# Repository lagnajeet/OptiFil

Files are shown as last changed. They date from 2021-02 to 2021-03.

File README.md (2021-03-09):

# OptiFil
Optical Filament Sensor
<p align="center">
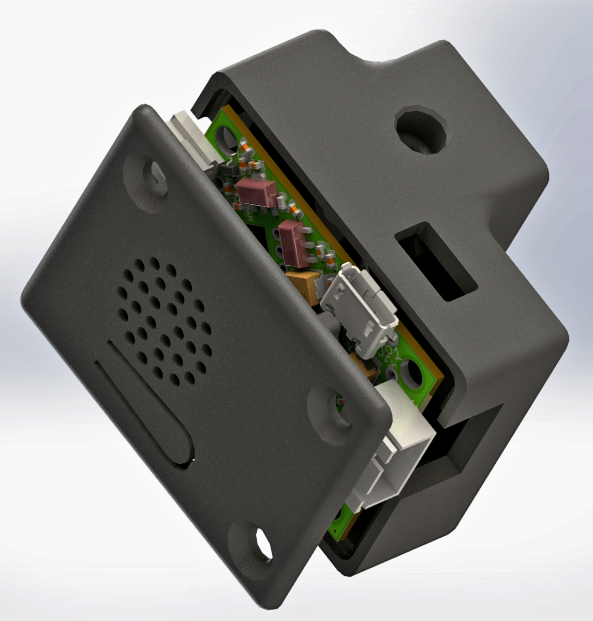
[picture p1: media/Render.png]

</p>
This filament sensor is based on the same principle that makes optical mouse work. The sennsor used in here is an ADNS9800 and the processor is an ESP8285. The filament moves infront of the optical mouse sensor and the surface property and speed of the sensor is used to determine runouts and jams.
<p align="center">

  <i>Green - Normal Operation, Red - Filament Runout, Purple - Filament Jammed</i>
</p>
The various settings of the sensor can be set from the web interface. The device exposes itself as a SSDP service.Below is a acreenshot of the web interface.
<p align="center">
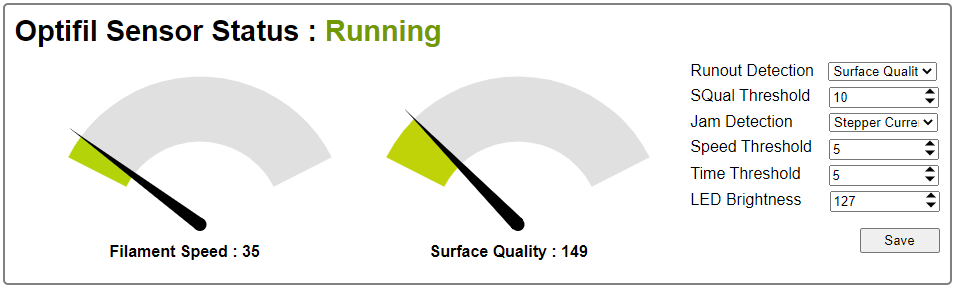
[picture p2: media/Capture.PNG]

</p>

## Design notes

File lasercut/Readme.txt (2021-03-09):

The SVG filles are for laser cutting the light guides and the edge light logo piece. The thickness of the acrylic is 2mm. The STL files are designed to take 2mm acrylics. Blacken the bottom surface with a very optically (which covers the IR range) opaque dye or material before putting the top cover.

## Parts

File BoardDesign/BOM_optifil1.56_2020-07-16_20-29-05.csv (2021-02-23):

ID | Name | Designator | Footprint | Quantity | Manufacturer Part | Manufacturer | Supplier | Supplier Part | value
1 | ESP8285_ESP-01F01F | U$3 | ESP8285-01F | 1 |  |  | LCSC |  | ESP8285_ESP-01F01F
2 | WS2812_2020 | LED3,LED4 | _2020 | 2 |  |  | LCSC
3 | SOLDERJUMPERNC | SJ1,SJ2 | SJ_2S_SMALL | 2 |  |  | LCSC |  | SOLDERJUMPERNC
4 | AVAGO_ADNS-9500 | U$1 | AVAGO_ADNS-9500 | 1 |  |  | LCSC |  | AVAGO_ADNS-9500
5 | 10u | C12,C14,C13,C15,C18,C5,C8,C6,C20,C24 | 402 | 10 |  |  | LCSC | C15525 | 10u
6 | 10k | R2,R3,R4,R1,R6,R7,R13,R14,R10,R15,R16 | 402 | 11 |  |  | LCSC | C25744 | 10k
7 | 100 | R5,R8 | 402 | 2 |  |  | LCSC | C25076 | 100
8 | JST-XH-03-PIN-ROUND-PAD | X1 | JST-XH-03-PACKAGE-ROUND-PAD | 1 |  |  | LCSC |  | JST-XH-03-PIN-ROUND-PAD
9 | 220uF 10V | C16,C17 | 3528-TE-B | 2 |  |  | LCSC | C110782 | 220uF 10V
10 | CP210X_USB_UART | IC4 | MLP28 | 1 |  |  | LCSC | C6568 | CP210X_USB_UART
11 | ME6119 | U$5 | SOT89 | 1 |  |  | LCSC | C82566 | ME6119
12 | 100n | C19,C23,C2,C9,C4 | 402 | 5 |  |  | LCSC | C1525 | 100n
13 | 1X01-CLEANBIG | JP1 | 1X01-CLEANBIG | 1 |  |  | LCSC
14 | 1u | C22,C1,C3,C11 | 402 | 4 |  |  | LCSC | C52923 | 1u
15 | 470p | C7 | 402 | 1 |  |  | LCSC | C1537 | 470p
16 | USBMICROB-PTH | USB1 | USB-MICROB-TH | 1 |  |  | LCSC |  | USBMICROB-PTH
17 | NTA4151PT1G | Q4 | SC75_INFINEON | 1 |  |  | LCSC | C54876 | NTA4151PT1G
18 | LEDSIDE | LED1,LED2 | LEDSIDE | 2 |  |  | LCSC
19 | CC6900SO-5A | U1 | SOIC127P600X175-8N | 1 |  |  | LCSC | C350864 | CC6900SO-5A
20 | 33k | R9 | 402 | 1 |  |  | LCSC | C25779 | 33k
21 | 1n | C10 | 402 | 1 |  |  | LCSC | C1523 | 1n
22 | 2N7002T | T3,T4,T5 | SOT416 | 3 |  |  | LCSC | C248732 | 2N7002T
23 | C8598 | D1 | SOD-123 | 1 |  |  | LCSC | C8598 | C8598
24 | TS-1187A-C-E-B | S2 | TACTILE_SWITCH_SMD_5.2MM | 1 |  |  | LCSC | C318886 | TS-1187A-C-E-B
25 | JST | J1 | CONN_S2B-PH-K-S_JST | 1 |  |  | LCSC |  | JST
26 | H7530-1_C277555 | IC1 | SOT23 | 1 |  |  | LCSC | C277555 | H7530-1_C277555

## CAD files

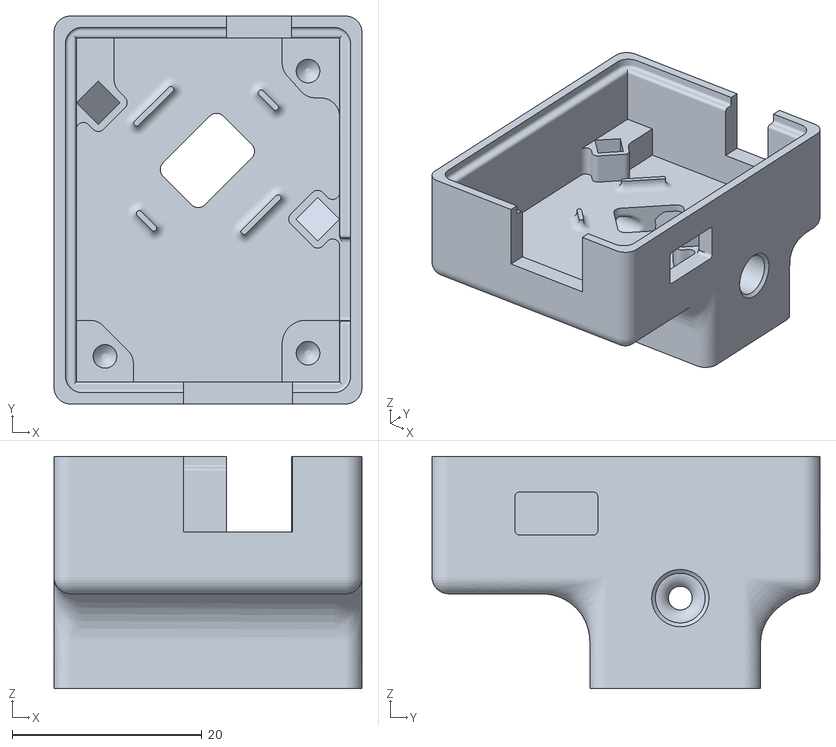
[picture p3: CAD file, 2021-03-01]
3DPrint/top_v2.19.STL
32.5 x 40.9 x 24.5

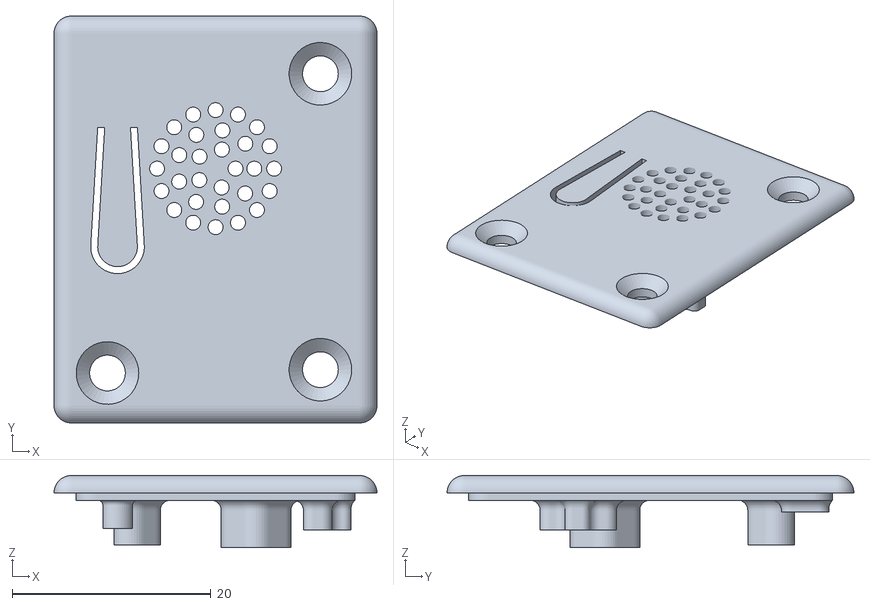
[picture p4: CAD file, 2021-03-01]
3DPrint/bottom1.7.STL
32.5 x 40.9 x 7.25

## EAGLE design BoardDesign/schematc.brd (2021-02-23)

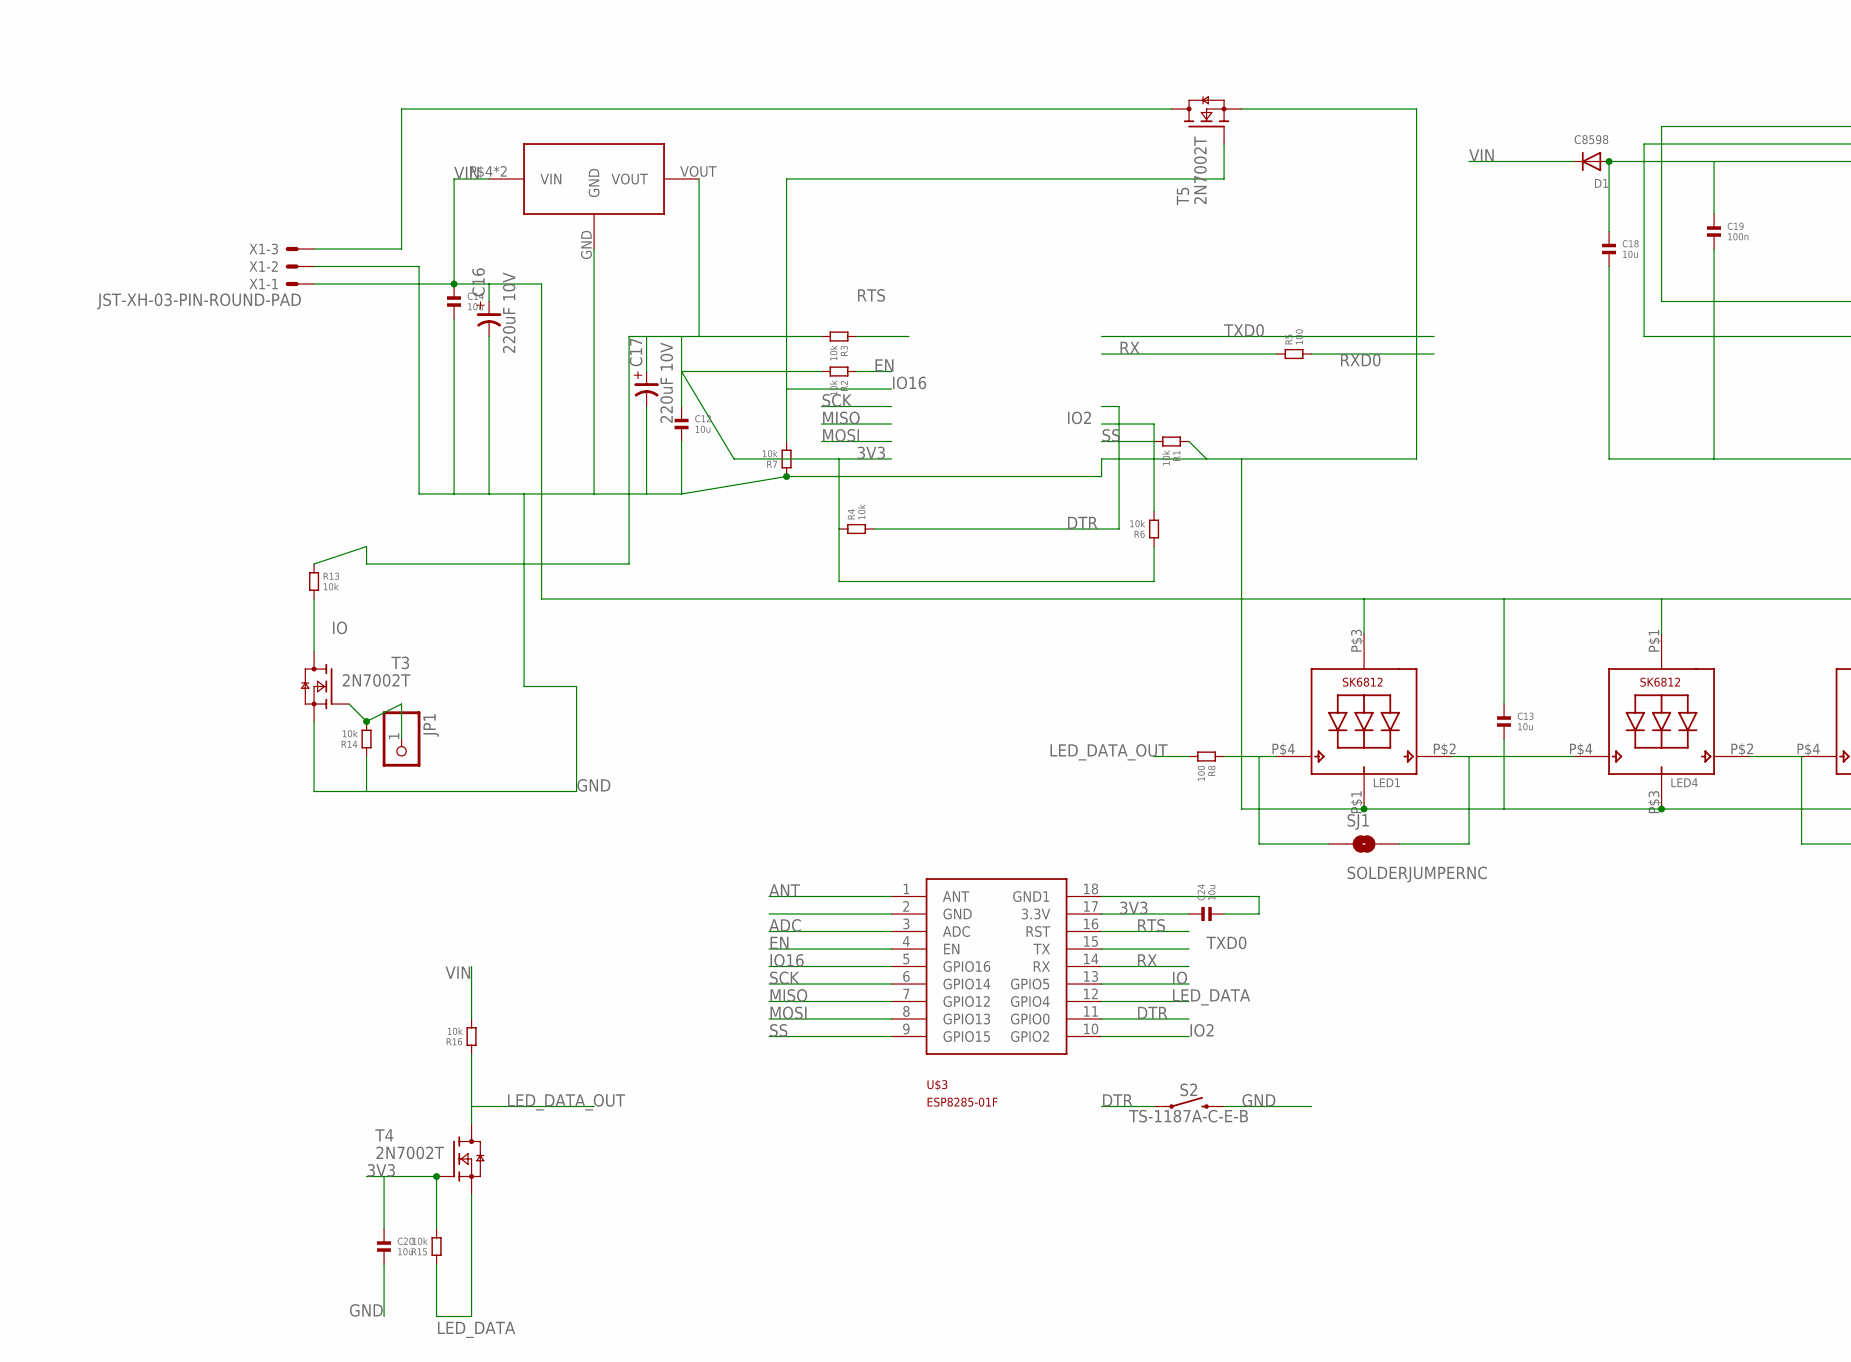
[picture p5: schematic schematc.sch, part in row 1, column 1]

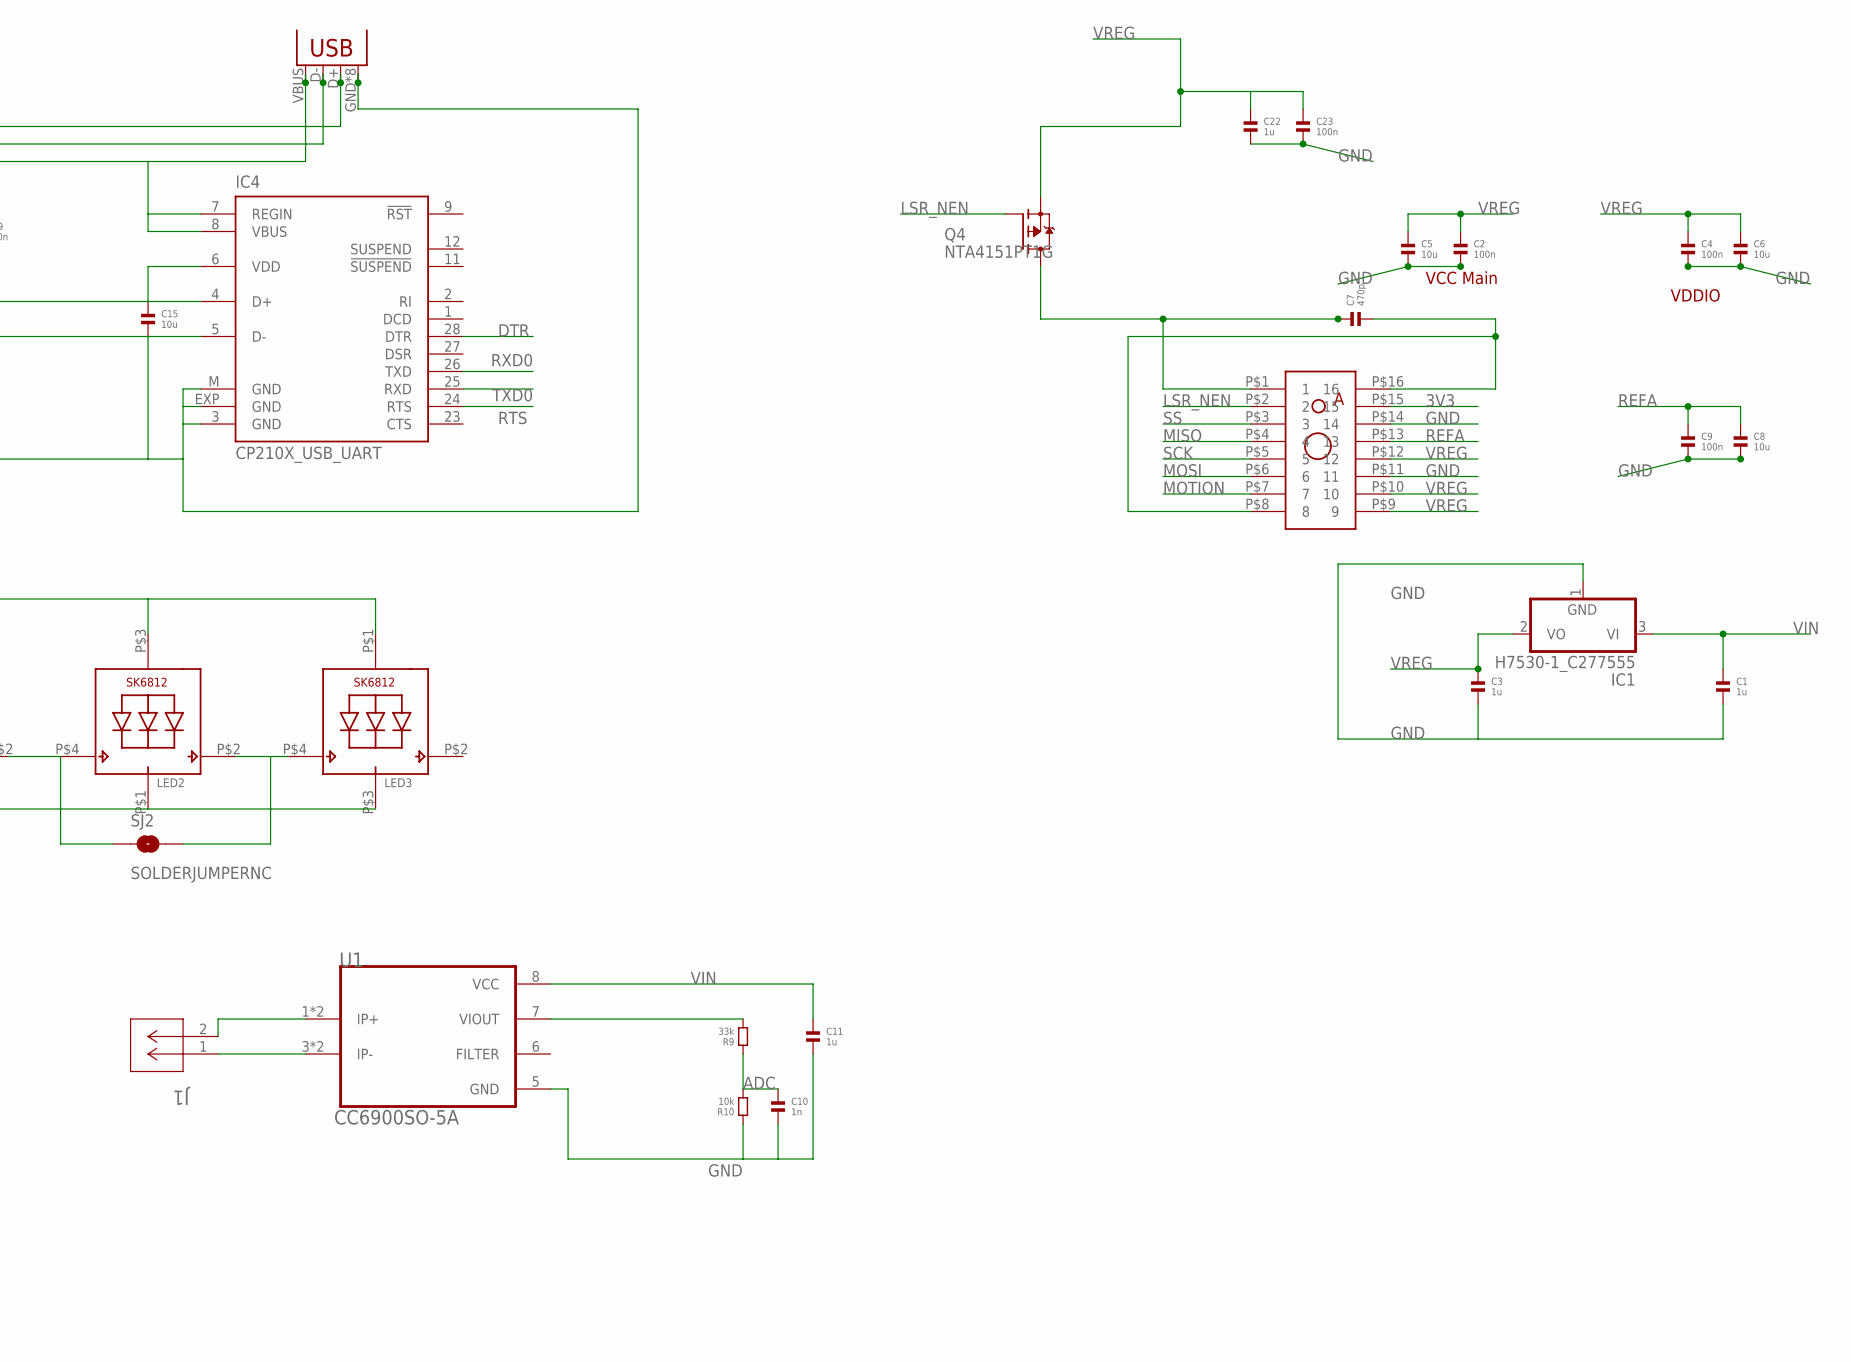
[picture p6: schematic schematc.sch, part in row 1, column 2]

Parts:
C1, C3, C11, C22: 1u; 0402
C2, C4, C9, C19, C23: 100n; 0402
C5, C6, C8, C12, C13, C14, C15, C18, C20, C24: 10u; 0402
C7: 470p; 0402
C10: 1n; 0402
C16, C17: 220uF 10V; 3528-TE-B
D1: C8598; SOD-123
IC1: H7530-1_C277555; SOT23
IC4: CP210X_USB_UART; MLP28
J1: JST; CONN_S2B-PH-K-S_JST
JP1: PINHD-1X1CB; 1X01-CLEANBIG
LED1, LED2: SK6812_SIDE; LEDSIDE
LED3, LED4: SK6812_2020; _2020
Q4: NTA4151PT1G; SC75_INFINEON
R1, R2, R3, R4, R6, R7, R10, R13, R14, R15, R16: 10k; 0402
R5, R8: 100; 0402
R9: 33k; 0402
S2: TS-1187A-C-E-B; TACTILE_SWITCH_SMD_5.2MM
SJ1, SJ2: SOLDERJUMPERNC; SJ_2S_SMALL
T3, T4, T5: 2N7002T; SOT416
U1: CC6900SO-5A; SOIC127P600X175-8N
U$1: AVAGO_ADNS-9500
U$3: ESP8285_ESP-01F01F; ESP8285-01F
U$5: ME6119; SOT89
USB1: USBMICROB-PTH; USB-MICROB-TH
X1: JST-XH-03-PIN-ROUND-PAD; JST-XH-03-PACKAGE-ROUND-PAD

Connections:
3V3: C12.1, C17.+, C20.1, C24.1, R2.2, R3.2, R4.1, R6.1, R13.1, R15.2, T4.1 (G), U$1.P$15 (15), U$3.17 (3.3V), U$5.VOUT
ADC: C10.1, R9.1, R10.2, U$3.3 (ADC)
ANT: U$3.1 (ANT)
DTR: IC4.28 (DTR), R4.2, S2.1, S2.2 (1), U$3.11 (GPIO0)
EN: R2.1, U$3.4 (EN)
GND: C1.2, C2.2, C3.2, C4.2, C5.2, C6.2, C8.2, C9.2, C10.2, C11.2, C12.2, C13.2, C14.2, C15.2, C16.-, C17.-, C18.2, C19.2, C20.2, C22.2, C23.2, C24.2, IC1.1 (GND), IC4.3 (GND), IC4.EXP (GND), IC4.M (GND), LED1.P$1 (GND), LED2.P$1 (GND), LED3.P$3 (GND), LED4.P$3 (GND), R1.1, R7.1, R10.1, R14.1, S2.3 (2), S2.4 (2), T3.2 (S), T5.2 (S), U1.5 (GND), U$1.P$11 (11), U$1.P$14 (14), U$3.2 (GND), U$3.18 (GND1), U$5.GND, USB1.GND, USB1.ID (GND), USB1.M5 (GND), USB1.M6 (GND), USB1.MT1 (GND), USB1.MT2 (GND), USB1.MT3 (GND), USB1.MT4 (GND), X1.2
IO: R13.2, T3.3 (D), U$3.13 (GPIO5)
IO2: R6.2, U$3.10 (GPIO2)
IO16: R7.2, T5.1 (G), U$3.5 (GPIO16)
LED_DATA: R15.1, T4.2 (S), U$3.12 (GPIO4)
LED_DATA_OUT: R8.2, R16.1, T4.3 (D)
LSR_NEN: Q4.1 (G), U$1.P$2 (2)
MISO: U$1.P$4 (4), U$3.7 (GPIO12)
MOSI: U$1.P$6 (6), U$3.8 (GPIO13)
MOTION: U$1.P$7 (7)
unnamed: C7.2, U$1.P$8 (8), U$1.P$16 (16)
unnamed: C7.1, Q4.2 (D), U$1.P$1 (1)
unnamed: J1.2, U1.1 (IP+), U1.2 (IP+)
unnamed: J1.1, U1.3 (IP-), U1.4 (IP-)
unnamed: R9.2, U1.7 (VIOUT)
unnamed: LED1.P$2 (DO), LED4.P$4 (DI), SJ1.2
unnamed: LED1.P$4 (DI), R8.1, SJ1.1
unnamed: LED2.P$2 (DO), LED3.P$4 (DI), SJ2.2
unnamed: LED2.P$4 (DI), LED4.P$2 (DO), SJ2.1
unnamed: JP1.1, R14.2, T3.1 (G)
unnamed: T5.3 (D), X1.3
unnamed: C18.1, C19.1, D1.A, IC4.7 (REGIN), IC4.8 (VBUS), USB1.VBUS
unnamed: C15.1, IC4.6 (VDD)
unnamed: IC4.5 (D-), USB1.D-
unnamed: IC4.4 (D+), USB1.D+
REFA: C8.1, C9.1, U$1.P$13 (13)
RTS: IC4.24 (RTS), R3.1, U$3.16 (RST)
RX: R5.1, U$3.14 (RX)
RXD0: IC4.26 (TXD), R5.2
SCK: U$1.P$5 (5), U$3.6 (GPIO14)
SS: R1.2, U$1.P$3 (3), U$3.9 (GPIO15)
TXD0: IC4.25 (RXD), U$3.15 (TX)
VIN: C1.1, C11.1, C13.1, C14.1, C16.+, D1.C, IC1.3 (VI), LED1.P$3 (VDD), LED2.P$3 (VDD), LED3.P$1 (VDD), LED4.P$1 (VDD), R16.2, U1.8 (VCC), U$5.P$4 (VIN), U$5.VIN, X1.1
VREG: C2.1, C3.1, C4.1, C5.1, C6.1, C22.1, C23.1, IC1.2 (VO), Q4.3 (S), U$1.P$9 (9), U$1.P$10 (10), U$1.P$12 (12)

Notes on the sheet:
VDDIO
VCC Main

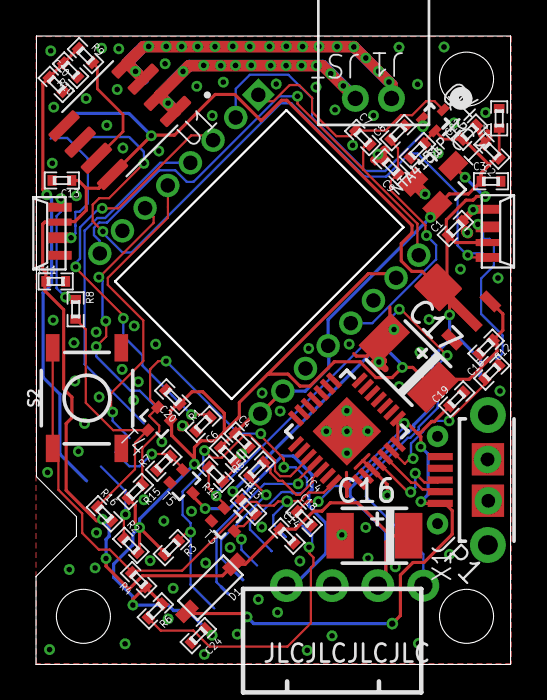
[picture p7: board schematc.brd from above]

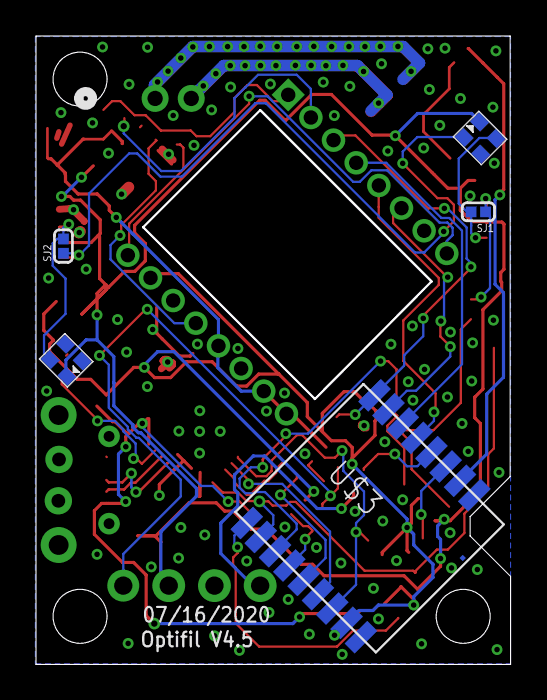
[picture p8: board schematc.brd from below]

Board: 2 copper layers, 26.4 x 34.9 mm, 59 parts (5 on the bottom side), 37 nets.

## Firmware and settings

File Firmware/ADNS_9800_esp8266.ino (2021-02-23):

#include <ArduinoQueue.h>
#include <SimpleCLI.h>
#include <CommandHandler.h>
#include <ArduinoTimer.h>
#include <ESP8266WiFi.h>          //ESP8266 Core WiFi Library (you most likely already have this in your sketch)

#include <DNSServer.h>            //Local DNS Server used for redirecting all requests to the configuration portal
#include <ESP8266WebServer.h>     //Local WebServer used to serve the configuration portal
#include <WiFiManager.h>          //https://github.com/tzapu/WiFiManager WiFi Configuration Magic
#include <ESP8266SSDP.h>
#include <ESP8266mDNS.h>        // Include the mDNS library

#include <SPI.h>

#include <Adafruit_NeoPixel.h>

#include <avr/pgmspace.h>
#include <FS.h>
const int sensorPin = A0;  // ESP8266 Analog Pin ADC0 = A0

// Registers
#define REG_Product_ID                           0x00
#define REG_Revision_ID                          0x01
#define REG_Motion                               0x02
#define REG_Delta_X_L                            0x03
#define REG_Delta_X_H                            0x04
#define REG_Delta_Y_L                            0x05
#define REG_Delta_Y_H                            0x06
#define REG_SQUAL                                0x07
#define REG_Pixel_Sum                            0x08
#define REG_Maximum_Pixel                        0x09
#define REG_Minimum_Pixel                        0x0a
#define REG_Shutter_Lower                        0x0b
#define REG_Shutter_Upper                        0x0c
#define REG_Frame_Period_Lower                   0x0d
#define REG_Frame_Period_Upper                   0x0e
#define REG_Configuration_I                      0x0f
#define REG_Configuration_II                     0x10
#define REG_Frame_Capture                        0x12
#define REG_SROM_Enable                          0x13
#define REG_Run_Downshift                        0x14
#define REG_Rest1_Rate                           0x15
#define REG_Rest1_Downshift                      0x16
#define REG_Rest2_Rate                           0x17
#define REG_Rest2_Downshift                      0x18
#define REG_Rest3_Rate                           0x19
#define REG_Frame_Period_Max_Bound_Lower         0x1a
#define REG_Frame_Period_Max_Bound_Upper         0x1b
#define REG_Frame_Period_Min_Bound_Lower         0x1c
#define REG_Frame_Period_Min_Bound_Upper         0x1d
#define REG_Shutter_Max_Bound_Lower              0x1e
#define REG_Shutter_Max_Bound_Upper              0x1f
#define REG_LASER_CTRL0                          0x20
#define REG_Observation                          0x24
#define REG_Data_Out_Lower                       0x25
#define REG_Data_Out_Upper                       0x26
#define REG_SROM_ID                              0x2a
#define REG_Lift_Detection_Thr                   0x2e
#define REG_Configuration_V                      0x2f
#define REG_Configuration_IV                     0x39
#define REG_Power_Up_Reset                       0x3a
#define REG_Shutdown                             0x3b
#define REG_Inverse_Product_ID                   0x3f
#define REG_Snap_Angle                           0x42
#define REG_Motion_Burst                         0x50
#define REG_SROM_Load_Burst                      0x62
#define REG_Pixel_Burst                          0x64

byte initComplete=0;
byte testctr=0;
unsigned long currTime;
unsigned long timer;
unsigned long pollTimer;
unsigned long debounceTime=0;
volatile int xydat[2];
volatile int Squal;
volatile byte movementflag=0;
const int ncs = 15;   //this is the slave select pin
const int button1 = 5;		//External Input
const int button0 = 0;		//Enable disbale button
const int jamLed = 4;
const int runoutLed = 2;    //This is inverted
const int notifyPin = 16;   //this is active low in CR-10 i.e. low means ok and high means problem
const unsigned short firmware_length = 3070;

int zeroSpeedTh=5;			// Line 1 , Specifies which line in the settings file has value for this variable
int zeroSpeedTime=10;		// Line 2
int minSqVal = 5;			// Line 3
int LEDBrightness = 16;		// Line 4 this number decides the brightnes of the indicator LED. 0 means disabled and any other number means that much brighness
//int ExternalInput = 0;		//Line 5 if enabled it listens to external signal for turning sensing on.
int JamDetection = 0;		//Line 5 Enable Jam detection if not set to 0
int RunOutDetection = 1;	//Line 6 Enable runout detection if set to 1 

uint8_t CurrentSensorValue = 0;		//Hall effect current sensorvalue
int incomingByte = 0;
#define QUEUE_SIZE_ITEMS 512
uint8_t currentQueue[QUEUE_SIZE_ITEMS] = { 0 };
int currentSensnorCount = 0;
long xDist = 0;
long yDist = 0;
bool tempLigh = true;
long rdist = 0;
long rspeed = 0;
int rspeedBelowTh = 0;
int rspeedCheckCount = 0;
long temprdist = 0;
int distCount = 0;
int samplingPeriod = 10;  //in ms
bool jammed = false;
bool runout = false;
bool startMonitoring = true;
int globalR, globalG, globalB;
bool prevButton0State = true;
int longpressCounter = 0;

SPISettings ADNS(1500000, MSBFIRST, SPI_MODE3);
#define numLEDS 2
#define MAXDIFFERENCE 25
#define MAXVARIANCE 15
Adafruit_NeoPixel strip = Adafruit_NeoPixel(numLEDS, jamLed, NEO_GRB + NEO_KHZ800);
static const char ispinJs[] PROGMEM = "!function(t,e){\"object\"==typeof exports&&\"undefined\"!=typeof module?module.exports=e():\"function\"==typeof define&&define.amd?define(e):t.ISpin=e()}(this,function(){\"use strict\";function t(t,e){for(var n=0;n<e.length;n++){var s=e[n];s.enumerable=s.enumerable||!1,s.configurable=!0,\"value\"in s&&(s.writable=!0),Object.defineProperty(t,s.key,s)}}function e(t,e,n){return e in t?Object.defineProperty(t,e,{value:n,enumerable:!0,configurable:!0,writable:!0}):t[e]=n,t}function n(){return(n=Object.assign||function(t){for(var e=1;e<arguments.length;e++){var n=arguments[e];for(var s in n)Object.prototype.hasOwnProperty.call(n,s)&&(t[s]=n[s])}return t}).apply(this,arguments)}function s(t){return function(t){if(Array.isArray(t)){for(var e=0,n=new Array(t.length);e<t.length;e++)n[e]=t[e];return n}}(t)||function(t){if(Symbol.iterator in Object(t)||\"[object Arguments]\"===Object.prototype.toString.call(t))return Array.from(t)}(t)||function(){throw new TypeError(\"Invalid attempt to spread non-iterable instance\")}()}var i=function(){function i(t,e){!function(t,e){if(!(t instanceof e))throw new TypeError(\"Cannot call a class as a function\")}(this,i),this.el=t,this.options={},this._onKeyDown=this._onKeyDown.bind(this),this._onMouseDown=this._onMouseDown.bind(this),this._onMouseUp=this._onMouseUp.bind(this),this._onMouseLeave=this._onMouseLeave.bind(this),this._onWheel=this._onWheel.bind(this),this.build(),this.update(e)}var r,a,p;return r=i,(a=[{key:\"build\",value:function(){var t=this;this._wrapper=document.createElement(\"div\"),this.el.parentNode&&this.el.parentNode.replaceChild(this._wrapper,this.el),this._wrapper.appendChild(this.el),this._buttons={inc:document.createElement(\"button\"),dec:document.createElement(\"button\")},Object.keys(this._buttons).forEach(function(e){var n=t._buttons[e];t._wrapper.appendChild(n),n.setAttribute(\"type\",\"button\"),n.addEventListener(\"mousedown\",t._onMouseDown),n.addEventListener(\"mouseup\",t._onMouseUp),n.addEventListener(\"mouseleave\",t._onMouseLeave)}),this.el.addEventListener(\"keydown\",this._onKeyDown),this.el.addEventListener(\"wheel\",this._onWheel)}},{key:\"update\",value:function(t){var s=this;(t=function(t){for(var n=1;n<arguments.length;n++){var s=null!=arguments[n]?arguments[n]:{},i=Object.keys(s);\"function\"==typeof Object.getOwnPropertySymbols&&(i=i.concat(Object.getOwnPropertySymbols(s).filter(function(t){return Object.getOwnPropertyDescriptor(s,t).enumerable}))),i.forEach(function(n){e(t,n,s[n])})}return t}({},i.DEFAULTS,this.options,t)).wrapperClass!==this.options.wrapperClass&&(this.options.wrapperClass&&this._wrapper.classList.remove(this.options.wrapperClass),t.wrapperClass&&this._wrapper.classList.add(t.wrapperClass)),t.buttonsClass!==this.options.buttonsClass&&(this.options.buttonsClass&&Object.keys(this._buttons).forEach(function(t){s._buttons[t].classList.remove(s.options.buttonsClass),s._buttons[t].classList.remove(s.options.buttonsClass+\"-\"+t)}),t.buttonsClass&&Object.keys(this._buttons).forEach(function(e){s._buttons[e].classList.add(t.buttonsClass),s._buttons[e].classList.add(t.buttonsClass+\"-\"+e)})),this.disabled=t.disabled,n(this.options,t)}},{key:\"destroy\",value:function(){this._wrapper.parentNode&&this._wrapper.parentNode.replaceChild(this.el,this._wrapper),delete this.el,delete this._wrapper,delete this._buttons}},{key:\"_onKeyDown\",value:function(t){switch(t.keyCode){case 38:return t.preventDefault(),this.spin(this.options.step);case 40:return t.preventDefault(),this.spin(-this.options.step);case 33:return t.preventDefault(),this.spin(this.options.pageStep);case 34:return t.preventDefault(),this.spin(-this.options.pageStep)}}},{key:\"_onMouseDown\",value:function(t){t.preventDefault();var e=t.currentTarget===this._buttons.inc?1:-1;this.spin(e*this.options.step),this.el.focus(),this._startSpinning(e)}},{key:\"_onMouseUp\",value:function(t){this._stopSpinning()}},{key:\"_onMouseLeave\",value:function(t){this._stopSpinning()}},{key:\"_startSpinning\",value:function(t){var e=this;this._stopSpinning(),this._spinTimer=setInterval(function(){return e.spin(t*e.options.step)},this.options.repeatInterval)}},{key:\"_stopSpinning\",value:function(){clearInterval(this._spinTimer)}},{key:\"_onWheel\",value:function(t){if(document.activeElement===this.el){t.preventDefault();var e=t.deltaY>0?-1:1;this.spin(e*this.options.step)}}},{key:\"adjustValue\",value:function(t){return t=Number(t.toFixed(this.precision)),null!=this.options.max&&t>this.options.max&&(t=this.options.max),null!=this.options.min&&t<this.options.min&&(t=this.options.min),t}},{key:\"wrapValue\",value:function(t){return this.options.wrapOverflow&&null!=this.options.max&&null!=this.options.min&&(t<this.options.min?t=this.options.max:t>this.options.max&&(t=this.options.min)),t}},{key:\"spin\",value:function(t){this.value=this.adjustValue(this.wrapValue(this.value+t))}},{key:\"value\",get:function(){return this.options.parse(this.el.value)||0},set:function(t){var e=this.options.format(this.options.parse(String(t)));this.el.value=e,this.options.onChange&&this.options.onChange(e)}},{key:\"disabled\",get:function(){return this._buttons.inc.disabled},set:function(t){this.disabled!==t&&(this._buttons.inc.disabled=this._buttons.dec.disabled=t)}},{key:\"precision\",get:function(){return Math.max.apply(Math,s([this.options.step,this.options.min].filter(function(t){return null!=t}).map(o)))}}])&&t(r.prototype,a),p&&t(r,p),i}();function o(t){return(String(t).split(\".\")[1]||\"\").length}return i.DEFAULTS={wrapperClass:\"ispin-wrapper\",buttonsClass:\"ispin-button\",step:1,pageStep:10,disabled:!1,repeatInterval:200,wrapOverflow:!1,parse:Number,format:String},i});";
static const char ispinCss[] PROGMEM = ".ispin-wrapper{position:relative;display:inline-block;overflow:hidden;padding:0;vertical-align:middle}.ispin-wrapper .ispin-button{position:absolute;display:block;height:60%;min-height:0;min-width:0;width:18px;padding:0;margin:0;right:0;border:none;background:0 0;cursor:pointer}.ispin-wrapper .ispin-button:before{content:'';display:inline-block;-webkit-transform:translateY(-50%);transform:translateY(-50%);border-left:5px solid transparent;border-right:5px solid transparent}.ispin-wrapper .ispin-button.ispin-button-inc{top:0}.ispin-wrapper .ispin-button.ispin-button-inc:before{border-bottom:5px solid #000}.ispin-wrapper .ispin-button.ispin-button-inc:disabled:before{border-bottom-color:grey}.ispin-wrapper .ispin-button.ispin-button-dec{bottom:0}.ispin-wrapper .ispin-button.ispin-button-dec:before{border-top:5px solid #000}.ispin-wrapper .ispin-button.ispin-button-dec:disabled:before{border-top-color:grey}";
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
void loop() 
{
    currTime = millis();
    server.handleClient();    
	// Check if user typed something into the serial monitor
	if (Serial.available()) {
		// Read out string from the serial monitor
		String input = Serial.readStringUntil('\n');

		// Echo the user input
		Serial.print("# ");
		Serial.println(input);

		// Parse the user input into the CLI
		cli.parse(input);
	}

	if (cli.errored()) {
		CommandError cmdError = cli.getError();

		Serial.print("ERROR: ");
		Serial.println(cmdError.toString());

		if (cmdError.hasCommand()) {
			Serial.print("Did you mean \"");
			Serial.print(cmdError.getCommand().toString());
			Serial.println("\"?");
		}
	}
    if(currTime > pollTimer)
    {
        if(currTime > debounceTime)
        {
          if(!digitalRead(button0))
          {
			  if (prevButton0State)
			  {
				  startMonitoring = !startMonitoring;
				  RunOutDetection = (startMonitoring ? 1 : 0);
				  Serial.println("Button0 pressed : " + String(startMonitoring));
			  }
			  prevButton0State = false;
			  longpressCounter++;
			  if (longpressCounter >= 50)
			  {
				  Serial.println("Clear WiFi passwords");
				  WiFi.disconnect(true);
				  setLedColor(0, 0, 1);
				  delay(2000);
				  ESP.reset();
				  longpressCounter = 0;
			  }
          }
		  else
		  {
			  prevButton0State = true;
			  longpressCounter = 0;
		  }
		  //if (!digitalRead(button1))
		  //{
			 // Serial.println("Button1 pressed : ");
		  //}
          debounceTime=currTime+100;
        }
        if(!configMode)
        {
          if(!serverUp)
          {
            server.begin();                           // Actually start the server
            IPAddress ip; 
            ip = WiFi.localIP();
            String ipString = String(ip[0]);
            for (byte octet = 1; octet < 4; ++octet) {
              ipString += '.' + String(ip[octet]);
            }            
            Serial.print("HTTP server started : ");
			Serial.println("http://" + String(ipString) + "/");
            serverUp=true;
            Serial.printf("Starting SSDP...\n");
            SSDP.setDeviceType("upnp:rootdevice");
            SSDP.setSchemaURL("description.xml");
            SSDP.setHTTPPort(80);
            SSDP.setName("Optifil Filament Sensor");
            SSDP.setSerialNumber(ESP.getChipId());
            SSDP.setURL("http://"+String(ipString)+"/");
            SSDP.setModelName("Optifil Sensor");
            SSDP.setModelNumber("929000226503");
            SSDP.setModelURL("http://www.optifil.com");
            SSDP.setManufacturer("LP Electronics");
            SSDP.setManufacturerURL("http://www.logicalside.com");
            SSDP.begin();         

			if (!MDNS.begin("optifil")) {             // Start the mDNS responder for optifil.local
				Serial.println("Error setting up MDNS responder!");
			}
			Serial.println("mDNS responder started");
          }
            
        }
        //digitalWrite(testpin, tempLigh);
        //digitalWrite(ledpin, !tempLigh);
        //tempLigh=!tempLigh;
		uint8_t tempsensnorval = (uint8_t)(analogRead(sensorPin)/4);
		memcpy(&currentQueue[1], &currentQueue[0], sizeof(uint8_t) * (QUEUE_SIZE_ITEMS - 1));
		currentQueue[0] = tempsensnorval;
		//if (currentQueue.isFull())
		//	currentQueue.dequeue();
		//currentQueue.enqueue(tempsensnorval);
		//if (tempsensnorval < curreftMin)
		//	curreftMin = tempsensnorval;
		//if (tempsensnorval > curreftMax)
		//	curreftMax = tempsensnorval;
		//curreftDFF = abs(curreftMax - curreftMin);
		//if (curreftDFF > 10)
		//	currentSensnorCount++;
		//else
		//{
		//	currentSensnorCount--;
		//	if (currentSensnorCount < 0)
		//		currentSensnorCount = 0;
		//}
		//for (int q = 0;q < QUEUE_SIZE_ITEMS;q++)
		//{
		//	Serial.printf("(%d, %d) ", q, currentQueue[q]);
		//}
		//uint8_t v = 0, d = 0;
		//CalcStats(&v, &d);
		//Serial.printf("(%d, %d)\n", v, d);
		//Serial.println(minMaxDifference());
		//Serial.println("\n_______________________________________");
		CurrentSensorValue = tempsensnorval;
        UpdatePointer();
        UpdateSqual();
        xydat[0] = convTwosComp(xydat[0]);
        xydat[1] = convTwosComp(xydat[1]);
        xDist=0;
        yDist=0;
        if(xydat[0] != 0 || xydat[1] != 0)
        {
            xDist=xydat[0];
            yDist=xydat[1];
        }
        if(Squal<= minSqVal && startMonitoring)	//start monitoring is enabled
        {
            setLedColor(1,0,0);
            runout=true;     
            digitalWrite(notifyPin, LOW);   
        }
        else
        {    
			if (startMonitoring)
			{
				runout = false;
				if (!jammed)
				{
					digitalWrite(notifyPin, HIGH);
					setLedColor(0, 1, 0);
				}
			}
			else		//if not monitoring then don't notify error and show a yellow LED
			{
				digitalWrite(notifyPin, HIGH);
				setLedColor(1, 1, 0);
			}
        }
        rdist = sqrt(  xDist*xDist +  yDist*yDist);    
        if(!runout)																			//do jam detection only if the filament has not run out i.e. runout is false
        {
          if(distCount<100)
          {
            temprdist=temprdist+rdist;
            distCount++;
          }
          else if(distCount>=100)
          {
            rspeed=temprdist;
            distCount=0;
            temprdist=0;          
            if(rspeed<zeroSpeedTh)
              rspeedBelowTh++;
            else
              rspeedBelowTh=0;
			uint8_t v = 0, d = 0;
			CalcStats(&v, &d);
            if(rspeedBelowTh>=zeroSpeedTime && JamDetection==1 && startMonitoring)			//if timeout based jam detection is enabled and start monitoring is enabled
            {
              rspeedBelowTh=zeroSpeedTime;
              setLedColor(1,0,2);
              jammed=true;
              digitalWrite(notifyPin, LOW);
            }
			else if (rspeedBelowTh >= zeroSpeedTime && JamDetection == 3 && d > MAXDIFFERENCE && v> MAXVARIANCE && startMonitoring)			//if current sensor based jam detection is enabled and start monitoring is enabled
			{
				rspeedBelowTh = zeroSpeedTime;
				setLedColor(1, 0, 2);
				jammed = true;
				digitalWrite(notifyPin, LOW);
			}
            else
            {
				if (startMonitoring)
				{
					setLedColor(0, 1, 0);
					jammed = false;
					digitalWrite(notifyPin, HIGH);
				}
				else		//if not monitoring then don't notify error and show a yellow LED
				{
					digitalWrite(notifyPin, HIGH);
					setLedColor(1, 1, 0);
				}
            }
          }
        }
        else
        {
          rspeedBelowTh=0;
        }
        pollTimer = currTime + 10;
    }

}

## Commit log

2021-02-23 schematic and layout files
    Eagle schematic and layout file along with the gerber file, BOM and PicknPlace file for manufacturing.
    [BOM_optifil1.56_2020-07-16_20-29-05.csv, PickAndPlace_optifil1.56_2020-07-16_20-29-37.csv, schematc.brd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]
2021-02-23 Firmware for Optical filament sensor
    Esp8285 firmware that run the OptiFil Sensor.
2021-03-01 Top and bottom 3D print STL Files
    [bottom1.7.STL, top_v2.19.STL]
2021-03-01 SVG files for Lasercut

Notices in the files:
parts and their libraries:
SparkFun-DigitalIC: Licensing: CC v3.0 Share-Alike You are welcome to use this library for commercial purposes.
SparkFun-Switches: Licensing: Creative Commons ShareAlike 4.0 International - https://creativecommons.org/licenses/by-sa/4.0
